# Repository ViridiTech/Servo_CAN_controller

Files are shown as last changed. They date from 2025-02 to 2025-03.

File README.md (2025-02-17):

# Servo_CAN_controller
Board allowing to turn DC motors into servomechanisms controlled by CAN bus using ESP32-C3 chip and AS5600 magnetic encoder

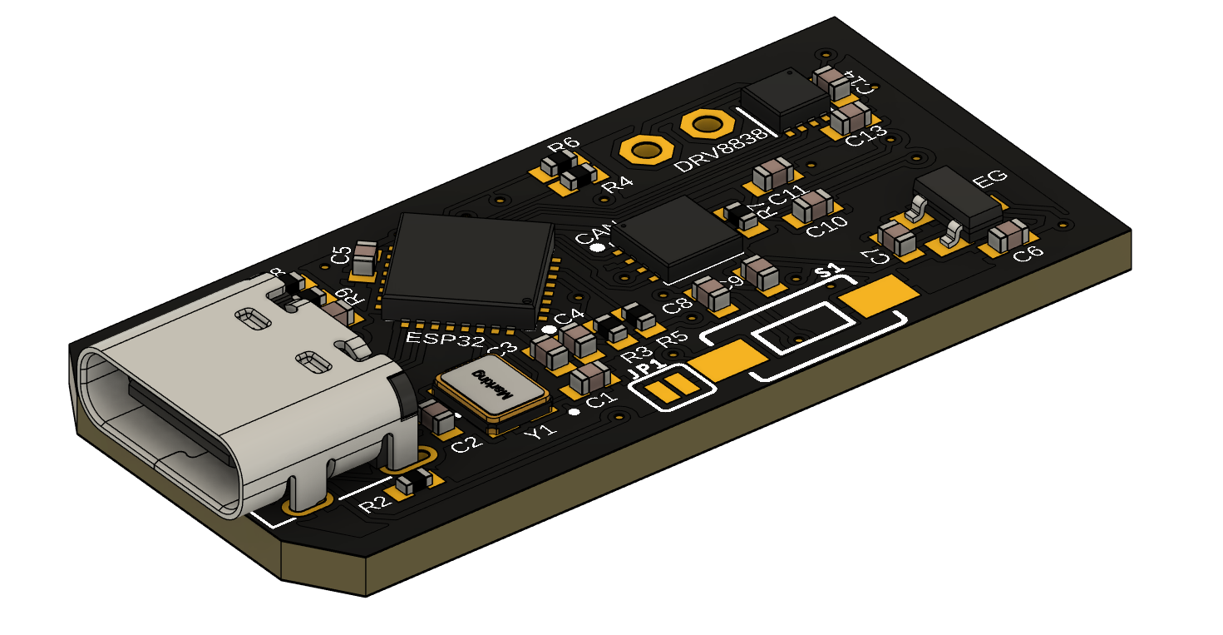
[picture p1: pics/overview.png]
</a>

This is the first version of ESP32-C3 microcontroller board with CAN transciever, DC motor driver (DRV8838) and magnetic encoder (AS5600). I will use it to control custom linear actuator.

# PCB layout
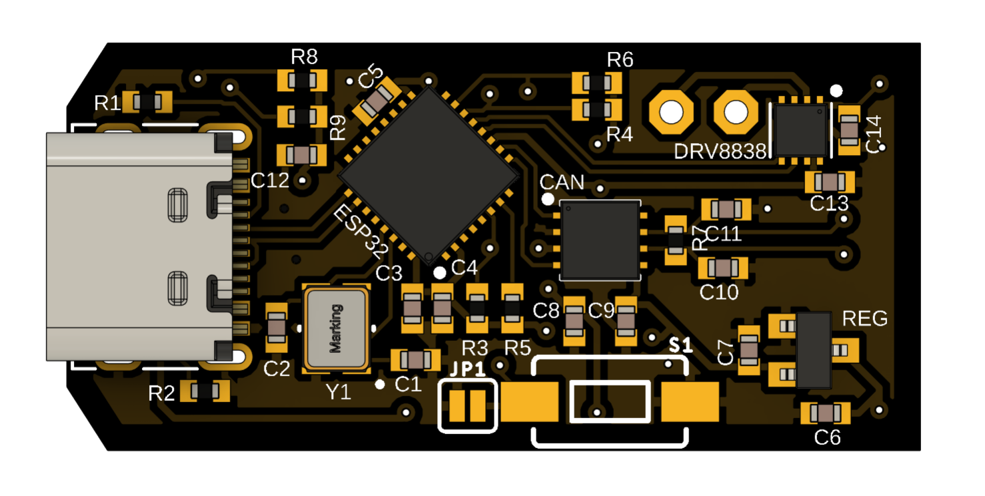
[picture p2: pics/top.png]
</a>
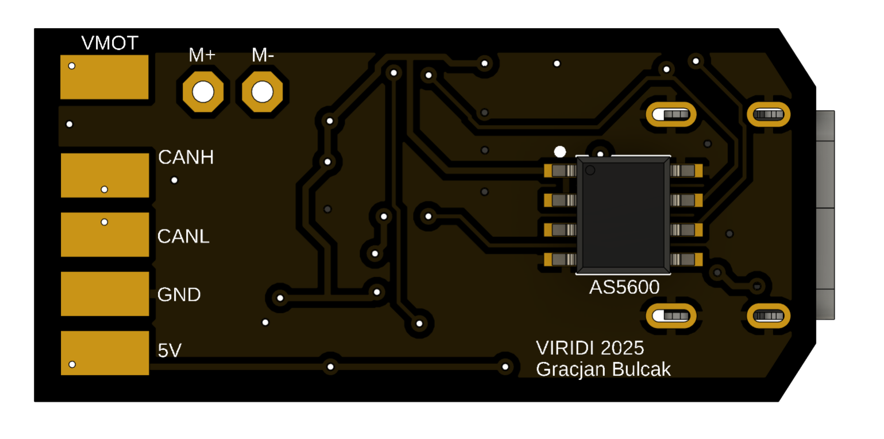
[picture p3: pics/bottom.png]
</a>

Top side has USB-C port, ESP32-C3FH4 chip, 40MHz crystal oscillator, CAN transciever module, 3.3V voltage regulator, DRV8838 DC motor driver and all passive components. Bottom side consists of breakout pads for power, ground and CAN lines and AS5600 magnetic ennoder

# Disclaimer
This board is yet to be assembled and tested.

I welcome you to discussion!

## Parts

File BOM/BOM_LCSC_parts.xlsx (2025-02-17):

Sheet: LCSC_Exported__20250218_010 (2)
LCSC Part Number | Manufacture Part Number | Manufacturer | Package | Description | Component/s | RoHS | Order Qty. | Unit Price($) | Order Price($)
C2858491 | ESP32-C3FH4 | Espressif Systems | QFN-32-EP(5x5) | QFN-32-EP(5x5) Microcontrollers (MCU/MPU/SOC) ROHS | ESP32 | YES | 1 | 1.8546 | 1.85
C86667 | DRV8838DSGR | Texas Instruments | WSON-8-EP(2x2) | WSON-8-EP(2x2) Brushed DC Motor Drivers ROHS | DRV8838 | YES | 1 | 0.5066 | 0.51
C5155979 | CA-IF1044VD-Q1 | Chipanalog | DFN-8(3x3) | DFN-8(3x3) CAN Transceivers ROHS | CAN | YES | 1 | 0.3060 | 0.31
C1545 | 0402CG100J500NT | FH (Guangdong Fenghua Advanced Tech) | 0402 | 50V 10pF C0G ±5% 0402 Multilayer Ceramic Capacitors MLCC - SMD/SMT ROHS | C1, C2 | YES | 2 | 0.0011 | 0.0022
C7472949 | HGC0402R5106M100NTEJ | Chinocera | 0402 | 10V 10uF X5R ±20% 0402 Multilayer Ceramic Capacitors MLCC - SMD/SMT ROHS | C3 | YES | 1 | 0.0063 | 0.01
C41851 | 0402B104K160NT | FH (Guangdong Fenghua Advanced Tech) | 0402 | 16V 100nF X7R ±10% 0402 Multilayer Ceramic Capacitors MLCC - SMD/SMT ROHS | C4, C5, C12, C13, C14 | YES | 5 | 0.0009 | 0.0045
C2887020 | TCC0402X5R105M100AT | CCTC | 0402 | 10V 1uF X5R ±20% 0402 Multilayer Ceramic Capacitors MLCC - SMD/SMT ROHS | C6, C7, C8, C9 | YES | 4 | 0.0016 | 0.01
C82219 | 0402B473K500NT | FH (Guangdong Fenghua Advanced Tech) | 0402 | 50V 47nF X7R ±10% 0402 Multilayer Ceramic Capacitors MLCC - SMD/SMT ROHS | C10, C11 | YES | 2 | 0.0017 | 0.0034
C453708 | RC-02K512JT | FH (Guangdong Fenghua Advanced Tech) | 0402 | Thick Film Resistors ±100ppm/℃ ±5% 5.1kΩ 0402 Chip Resistor - Surface Mount ROHS | R1, R2, R8, R9 | YES | 4 | 0.0003 | 0.0012
C25531 | 0402WGJ0103TCE | UNI-ROYAL(Uniroyal Elec) | 0402 | 62.5mW Thick Film Resistors 50V ±100ppm/℃ ±5% 10kΩ 0402 Chip Resistor - Surface Mount ROHS | R3, R4, R5, R6 | YES | 4 | 0.0005 | 0.002
C5446 | XC6206P332MR-G | Torex Semicon | SOT-23-3L | 200mA Fixed 3.3V Positive electrode 6V SOT-23-3L Voltage Regulators - Linear, Low Drop Out (LDO) Regulators ROHS | REG | YES | 1 | 0.0951 | 0.10
C22375371 | TS1101A26025 | HanElectricity | SMD,6x3.5mm | SMD,6x3.5mm Tactile Switches ROHS | S1 | YES | 1 | 0.0129 | 0.01
C9010 | X322540MPB4SI | YXC Crystal Oscillators | SMD3225-4P | 40MHz Surface Mount Crystal 15pF ±10ppm ±20ppm SMD3225-4P Crystals ROHS | Y1 | YES | 1 | 0.0805 | 0.08
C3017468 | SCR0402J120R | VO | 0402 | 62.5mW Thick Film Resistors 50V ±5% 120Ω 0402 Chip Resistor - Surface Mount ROHS | R7 | YES | 1 | 0.0005 | 0.0005
C136423 | MC-311D | SOFNG | SMD | 1 12P Female Type-C SMD USB Connectors ROHS | USB-C | YES | 1 | 0.1972 | 0.20
 |  |  |  |  |  |  |  | Sum amount: | 3.08

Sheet: LCSC_Exported__20250218_010732
LCSC Part Number,Manufacture Part Number,Manufacturer,Customer NO.,Package,Description,RoHS,Order Qty.,Min\Mult Order Qty.,Unit Price($),Order Price($)
C2858491,ESP32-C3FH4,Espressif Systems,,QFN-32-EP(5x5),QFN-32-EP(5x5) Microcontrollers (MCU/MPU/SOC) ROHS,YES,10,1\1,1.8546,18.55
C86667,DRV8838DSGR,Texas Instruments,,WSON-8-EP(2x2),WSON-8-EP(2x2) Brushed DC Motor Drivers ROHS,YES,10,1\1,0.5066,5.07
C5155979,CA-IF1044VD-Q1,Chipanalog,,DFN-8(3x3),DFN-8(3x3) CAN Transceivers ROHS,YES,10,1\1,0.306,3.06
C1545,0402CG100J500NT,FH (Guangdong Fenghua Advanced Tech),,0402,50V 10pF C0G Â±5% 0402 Multilayer Ceramic Capacitors MLCC - SMD/SMT ROHS,YES,100,100\100,0.0011,0.11
C7472949,HGC0402R5106M100NTEJ,Chinocera,,0402,10V 10uF X5R Â±20% 0402 Multilayer Ceramic Capacitors MLCC - SMD/SMT ROHS,YES,100,100\100,0.0063,0.63
C41851,0402B104K160NT,FH (Guangdong Fenghua Advanced Tech),,0402,16V 100nF X7R Â±10% 0402 Multilayer Ceramic Capacitors MLCC - SMD/SMT ROHS,YES,100,100\100,0.0009,0.09
C2887020,TCC0402X5R105M100AT,CCTC,,0402,10V 1uF X5R Â±20% 0402 Multilayer Ceramic Capacitors MLCC - SMD/SMT ROHS,YES,100,100\100,0.0016,0.16
C82219,0402B473K500NT,FH (Guangdong Fenghua Advanced Tech),,0402,50V 47nF X7R Â±10% 0402 Multilayer Ceramic Capacitors MLCC - SMD/SMT ROHS,YES,100,100\100,0.0017,0.17
C453708,RC-02K512JT,FH (Guangdong Fenghua Advanced Tech),,0402,Thick Film Resistors Â±100ppm/â„ƒ Â±5% 5.1kÎ© 0402 Chip Resistor - Surface Mount ROHS,YES,100,100\100,0.0003,0.03
C25531,0402WGJ0103TCE,UNI-ROYAL(Uniroyal Elec),,0402,62.5mW Thick Film Resistors 50V Â±100ppm/â„ƒ Â±5% 10kÎ© 0402 Chip Resistor - Surface Mount ROHS,YES,100,100\100,0.0005,0.05
C5446,XC6206P332MR-G,Torex Semicon,,SOT-23-3L,"200mA Fixed 3.3V Positive electrode 6V SOT-23-3L Voltage Regulators - Linear, Low Drop Out (LDO) Regulators ROHS",YES,10,5\5,0.0951,0.95
C22375371,TS1101A26025,HanElectricity,,"SMD,6x3.5mm","SMD,6x3.5mm Tactile Switches ROHS",YES,50,50\50,0.0129,0.65
C9010,X322540MPB4SI,YXC Crystal Oscillators,,SMD3225-4P,40MHz Surface Mount Crystal 15pF Â±10ppm Â±20ppm SMD3225-4P Crystals ROHS,YES,10,5\5,0.0805,0.81
C3017468,SCR0402J120R,VO,,0402,62.5mW Thick Film Resistors 50V Â±5% 120Î© 0402 Chip Resistor - Surface Mount ROHS,YES,100,100\100,0.0005,0.05
C136423,MC-311D,SOFNG,,SMD,1 12P Female Type-C SMD USB Connectors ROHS,YES,10,5\5,0.1972,1.97

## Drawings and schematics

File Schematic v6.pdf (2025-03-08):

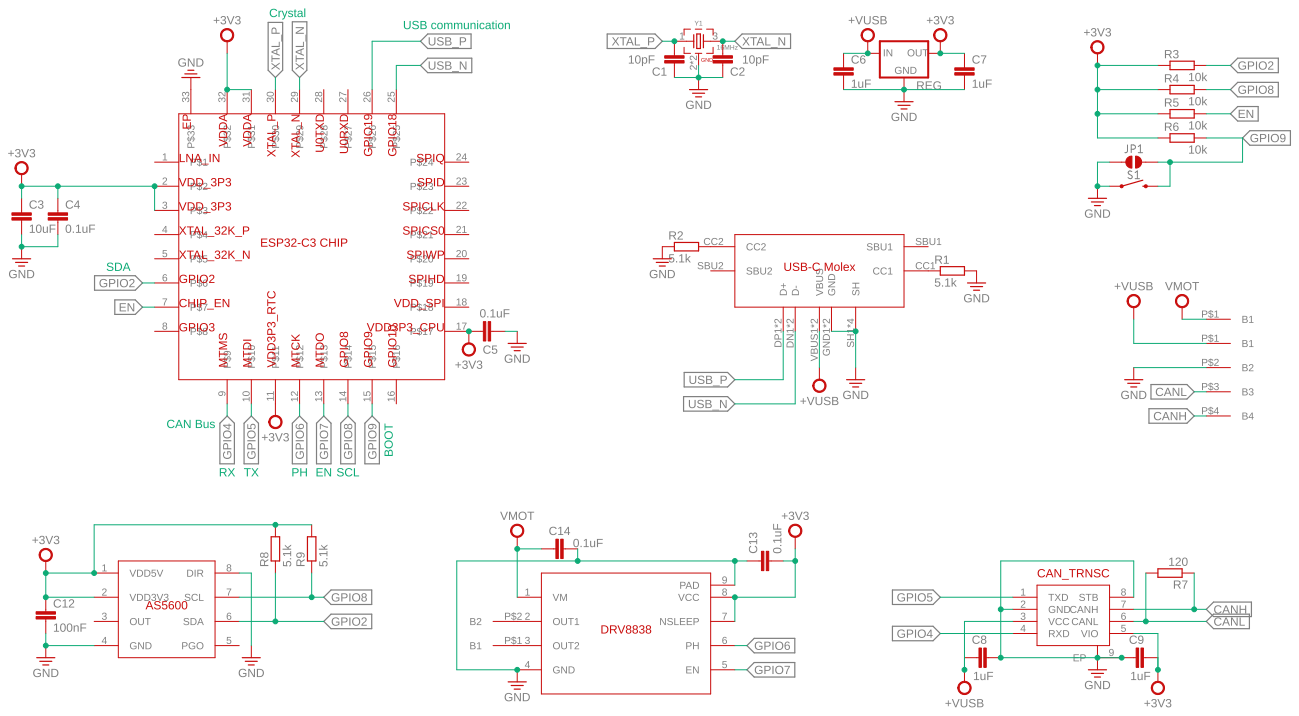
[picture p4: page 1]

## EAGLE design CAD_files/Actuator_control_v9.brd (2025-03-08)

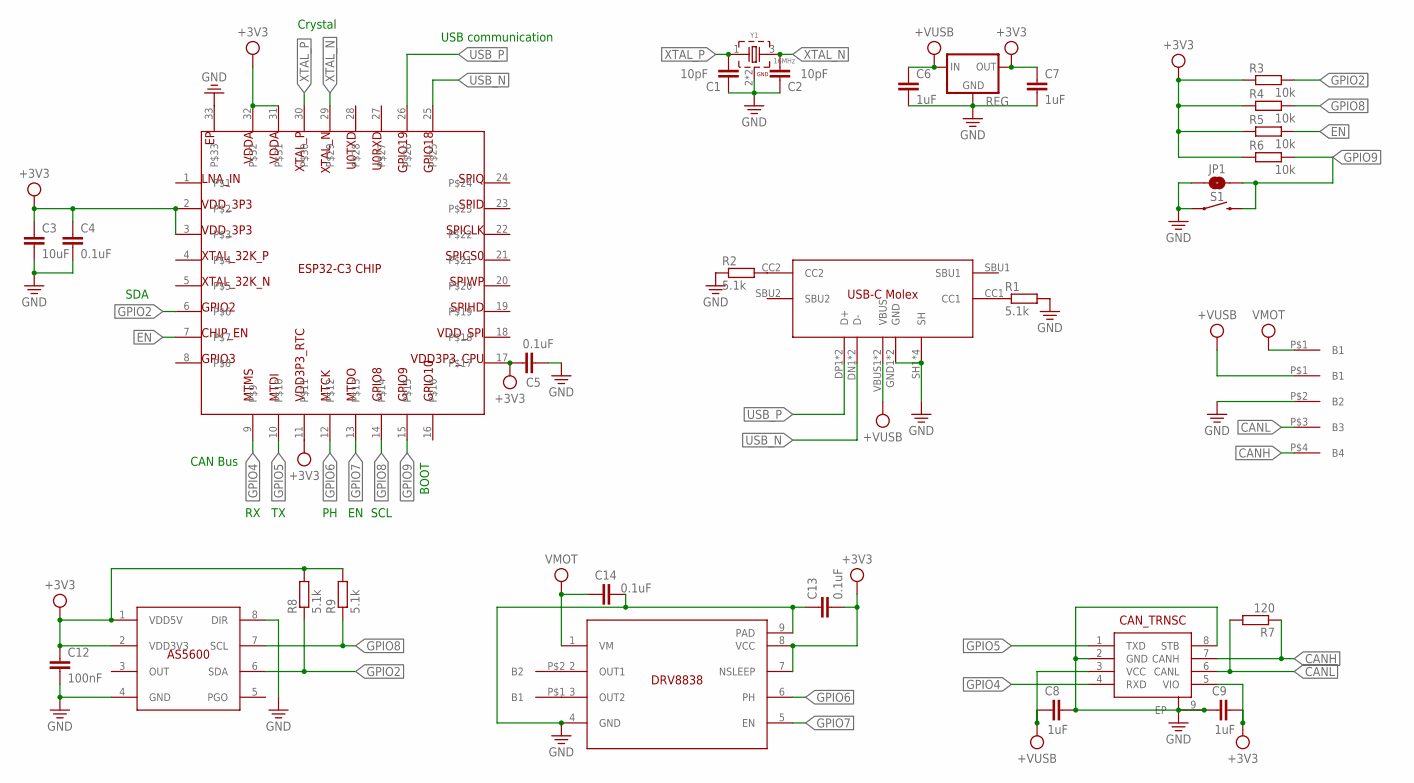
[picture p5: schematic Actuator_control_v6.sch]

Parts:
AS5600: AS5600; SOIC127P600X175-8N
C1, C2: 10pF; C0402
C3: 10uF; C0402
C4, C5, C13, C14: 0.1uF; C0402
C6, C7, C8, C9: 1uF; C0402
C12: 100nF; C0402
CAN: CAN_TRNSC; SON65P300X300X75-9T160X240N
DRV8838: DRV8838; SON50P200X200X80-9T90X160N
ESP32: ESP32-C3CHIP; ESP32-C3_CHIP
JP1: JUMPER-SMT_2_NO_SILK; SMT-JUMPER_2_NO_SILK
R1, R2, R8, R9: 5.1k; R0402
R3, R4, R5, R6: 10k; R0402
R7: 120; R0402
REG: XC63FPM; SOT23
S1: MOMENTARY-SWITCH-SPST-SMD-6.0X3.5MM; TACTILE_SWITCH_SMD_6.0X3.5MM
U$3: USB-CMOLEX
U$6: BREAKOUT_44-SMD2.54; BREAKOUT_4_SMD_2.54
U$7: BREAKOUT_11-SMD-2.54; BREAKOUT_1_SMD_2.54
U$8: BREAKOUT_22-THT; BREAKOUT_2_THT
Y1: 16MHz; WE-XTAL_CFPX-180

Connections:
+3V3: AS5600.1 (VDD5V), AS5600.2 (VDD3V3), C3.1, C4.1, C5.2, C7.1, C9.2, C12.1, C13.2, CAN.5 (VIO), DRV8838.7 (NSLEEP), DRV8838.8 (VCC), ESP32.2, ESP32.3, ESP32.11, ESP32.17, ESP32.31, ESP32.32, R3.1, R4.1, R5.1, R6.2, R8.2, R9.2, REG.2 (OUT)
+VUSB: C6.1, C8.1, CAN.3 (VCC), REG.3 (IN), U$3.VBUS1 (VBUS), U$3.VBUS2 (VBUS), U$6.P$1 (B1)
CANH: CAN.7 (CANH), R7.1, U$6.P$4 (B4)
CANL: CAN.6 (CANL), R7.2, U$6.P$3 (B3)
EN: ESP32.7, R5.2
GND: AS5600.4 (GND), AS5600.8 (DIR), C1.1, C2.1, C3.2, C4.2, C5.1, C6.2, C7.2, C8.2, C9.1, C12.2, C13.1, C14.2, CAN.2 (GND), CAN.8 (STB), CAN.9 (EP), DRV8838.4 (GND), DRV8838.9 (PAD), ESP32.33, JP1.1, R1.2, R2.1, REG.1 (GND), S1.1, U$3.GND1 (GND), U$3.GND2 (GND), U$3.SH1 (SH), U$3.SH2 (SH), U$3.SH3 (SH), U$3.SH4 (SH), U$6.P$2 (B2), Y1.2 (GND), Y1.4 (GND)
GPIO2: AS5600.6 (SDA), ESP32.6, R3.2, R8.1
GPIO4: CAN.4 (RXD), ESP32.9
GPIO5: CAN.1 (TXD), ESP32.10
GPIO6: DRV8838.6 (PH), ESP32.12
GPIO7: DRV8838.5 (EN), ESP32.13
GPIO8: AS5600.7 (SCL), ESP32.14, R4.2, R9.1
GPIO9: ESP32.15, JP1.2, R6.1, S1.2
unnamed: R1.1, U$3.CC1
unnamed: R2.2, U$3.CC2
unnamed: DRV8838.3 (OUT2), U$8.P$1 (B1)
unnamed: DRV8838.2 (OUT1), U$8.P$2 (B2)
OUT: AS5600.3 (OUT)
PGO: AS5600.5 (PGO)
USB_N: ESP32.25, U$3.DN1 (D-), U$3.DN2 (D-)
USB_P: ESP32.26, U$3.DP1 (D+), U$3.DP2 (D+)
VMOT: C14.1, DRV8838.1 (VM), U$7.P$1
XTAL_N: C2.2, ESP32.29, Y1.3 (2)
XTAL_P: C1.2, ESP32.30, Y1.1

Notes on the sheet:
USB communication
Crystal
CAN Bus
SCL
SDA
BOOT

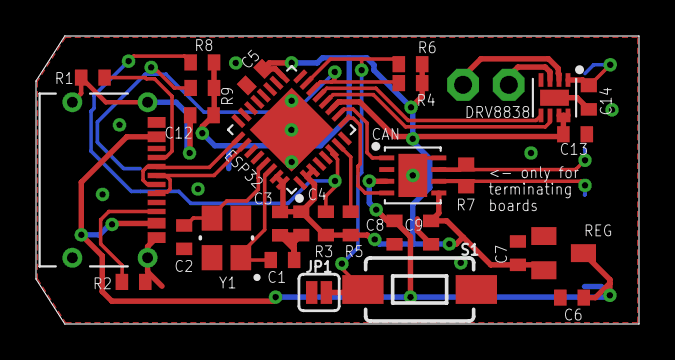
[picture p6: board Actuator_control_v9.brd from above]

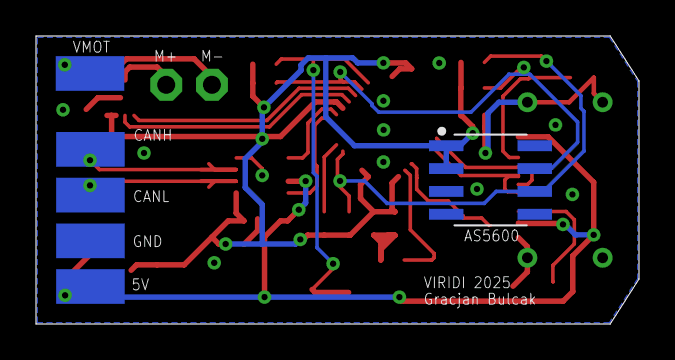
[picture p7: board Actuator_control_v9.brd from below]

Board: 2 copper layers, 33.5 x 16.0 mm, 33 parts (3 on the bottom side), 22 nets.

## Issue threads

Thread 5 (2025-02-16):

Components order

ViridiTech, 2025-02-16:
LCSC order
10x ESP32-C3FH4
10x DRV8838
10x CAN Transceiver
100x C0402 10pF
100x C0402 10uF
100x C0402 100nF
100x C0402 1uF
100x C0402 47nF
100x R0402 5.1k
100x R0402 10k
10x 3.3V LDO
50x Tactile switch 6x3.5mm
10x Crystal oscillator 40MHz
100x R0402 120
10x USB-C

Closed 2025-03-07.

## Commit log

2025-02-16 Rename Actuator control v6.pdf to Schematic v6.pdf
2025-02-16 Added CAD files
    [Actuator control v8.brd, Actuator_control_v6.sch]
2025-02-17 File ordering & BOM added
    [Actuator control v8.brd, Actuator_control_v6.sch, BOM_LCSC_parts.xlsx]
2025-03-07 Updated board
    Fixed Issue #8 "R1 is floating, not connected to GND"
    [Actuator_control_v9.brd]
2025-03-08 Resolved issue #9
    Removed CAN lines capacitors and added info regarding terminating resistors
    [Actuator_control_v6.sch, Actuator_control_v9.brd]

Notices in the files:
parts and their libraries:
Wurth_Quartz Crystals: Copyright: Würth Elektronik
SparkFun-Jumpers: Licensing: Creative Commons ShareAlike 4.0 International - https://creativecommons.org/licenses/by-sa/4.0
